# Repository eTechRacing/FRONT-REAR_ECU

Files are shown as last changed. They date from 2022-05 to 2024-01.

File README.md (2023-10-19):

# SHIELD

ADCAN files moved to ADCAN-Legacy branch

_Pendent de publicar en angles

La shield ha de ser una placa versàtil i robusta que serveixi per implementar fàcilment elements comuns que comparteixen diverses plaques. L’avantatge d’implementar una shield és la de disposar d’una base coneguda, provada i fiable per, 
a partir d’ella, implementar qualsevol altre sistema que s’hagi d’incloure dins del cotxe.
Les funcionalitats de la placa shield passen, principalment, per una alimentació estable i constant i per un bus de comunicacions amplament validat i funcional. 
Tot això rodejant d’un microcontrolador molt consistent encarregat de l’adquisició, el processament i l’enviament de dades.

Requisits:
-Alimentació a 5 V i 3.3 V a partir de LV
-Comunicació via CAN1 i CAN2
-Connectors plug-and-play
-MCU potent (STM23)
-Documentació
-Reduir EMIs i soroll amb un bon disseny

El conntector entre la shield i la carrier és una de les parts fonamentals de la placa. La idea és que hi hagi connexió electrica i mecànica entre elles.
S'opta per un connector board-to-board tipus pin header (fabricant Würth) ja que dona la opció d'encaixar una placa sobre l'altre i, a mes, de disposar de totes les connexions
amb un connector senzill de posar i treure.

El microcontrolador és el més potent que s'ha pogut aconseguir per patrocinadors. Més concretament el STM32F777VI6T que compleix de sobres tots els requisits. De totes maneres,
pensant en el fet de que la shield sigui una placa amb futur, s'afageix una memoria EEPROM utilitzat el I2C número 4 del STM32.

Pel que fa la resta de la placa no hi ha cap complicació. S'implementa un USB_OTG amb un connector micro USB 2.0 per debug i visualització de dades per PC. Es fa servir el CAN
transceiver MCP2551 de microchip (fàcil d'aconseguir per samples) i unes proteccions i filtres a la linea CAN bastant estàndard. La resta dels pins del MCU van directament al
pin header excepte:
-VBAT: es col·loca un divisor de tensió rebaixant 30V a 3.3V. Això permet fer servir VBAT com una entrada analogica per medir la tensió que ofereix la LV.
-VBUS: es fa servir com a entrada digital per detectar si hi ha presencia d'USB.
-NRST: pin de reset del micocontrolador. Necessari per programar. Se li posa un botó per també poder fer reset manualment.
-Boot0: se li posa un switch per curtcircuitar a 3.3V o a GND. Això permetrà setejar al micro com a blank i poder carregar informació des del USB o programar més facilment.

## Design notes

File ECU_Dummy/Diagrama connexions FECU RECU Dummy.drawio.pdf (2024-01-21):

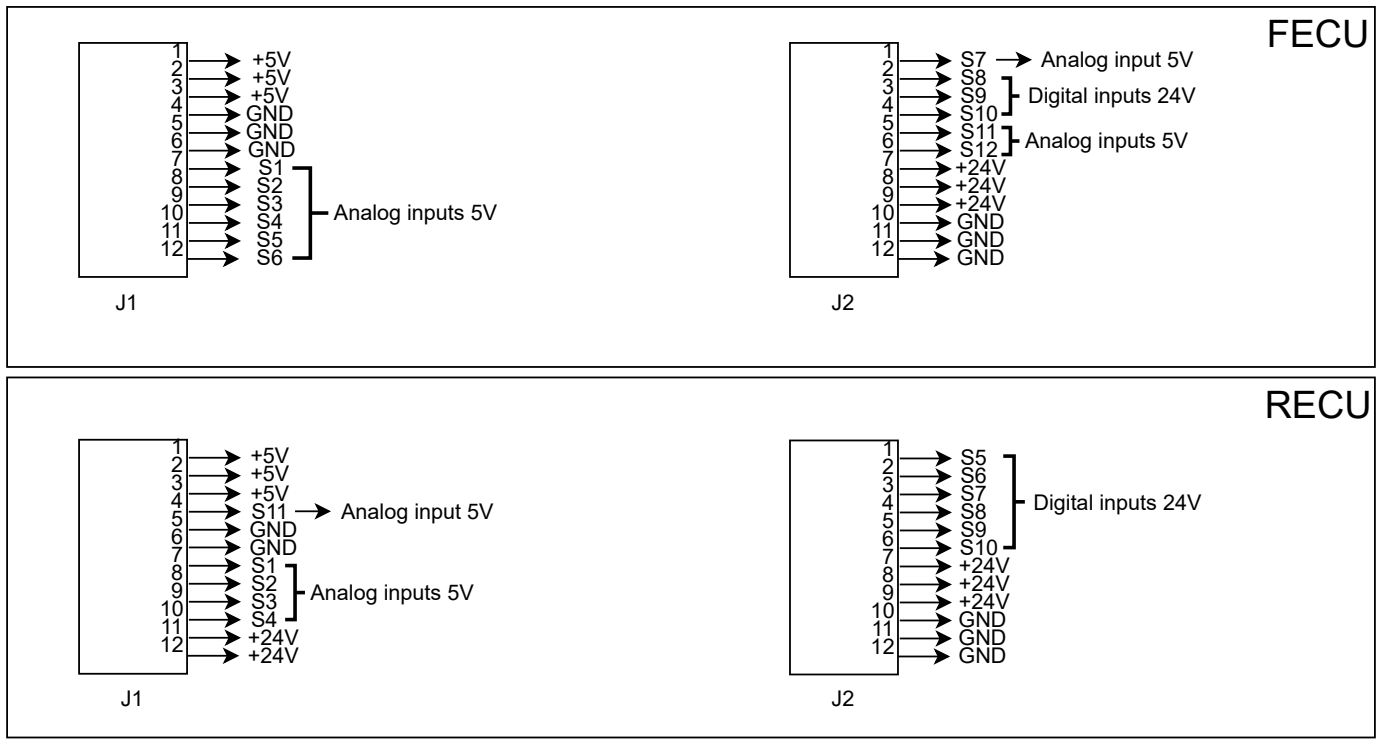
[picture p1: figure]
FECU; RECU; +5V +5V +5V GND GND GND S1 S2 S3 S4 S5 S6; Analog inputs 5V; S7 S8 S9 S10 S11 S12 +24V +24V +24V GND GND GND; Digital inputs 24V; S5 S6 S7 S8 S9 S10 +24V +24V +24V GND GND GND; +5V +5V +5V S11 GND GND S1 S2 S3 S4 +24V +24V; Analog input 5V
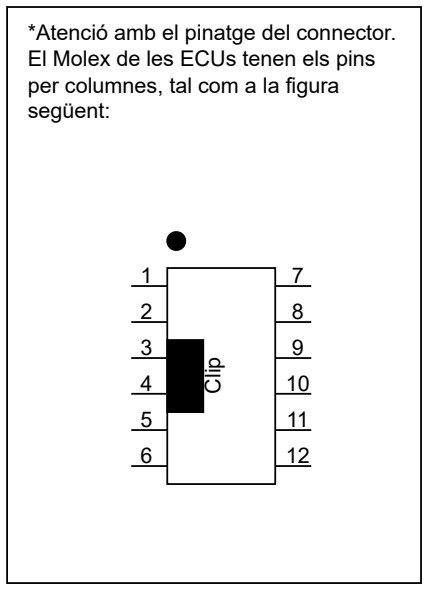
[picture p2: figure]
*Atenció amb el pinatge del connector. El Molex de les ECUs tenen els pins per columnes, tal com a la figura següent:; Clip

Taula connexions connectors des de les ECUs a ECU Dummy:

FRONT ECU

-J1 va a JFS1
-J2 va a JFRS2

REAR ECU

-J1 va a JRS1
-J2 va a JFRS2

*El connector JFRS2 es compatible amb el J2 de les dos ECUs. Nomes n'hi ha un a la ECU_Dummy per tant només es pot fer test del J2 a una ECU alhora

# ECUs & ECU_Dummy interconnections

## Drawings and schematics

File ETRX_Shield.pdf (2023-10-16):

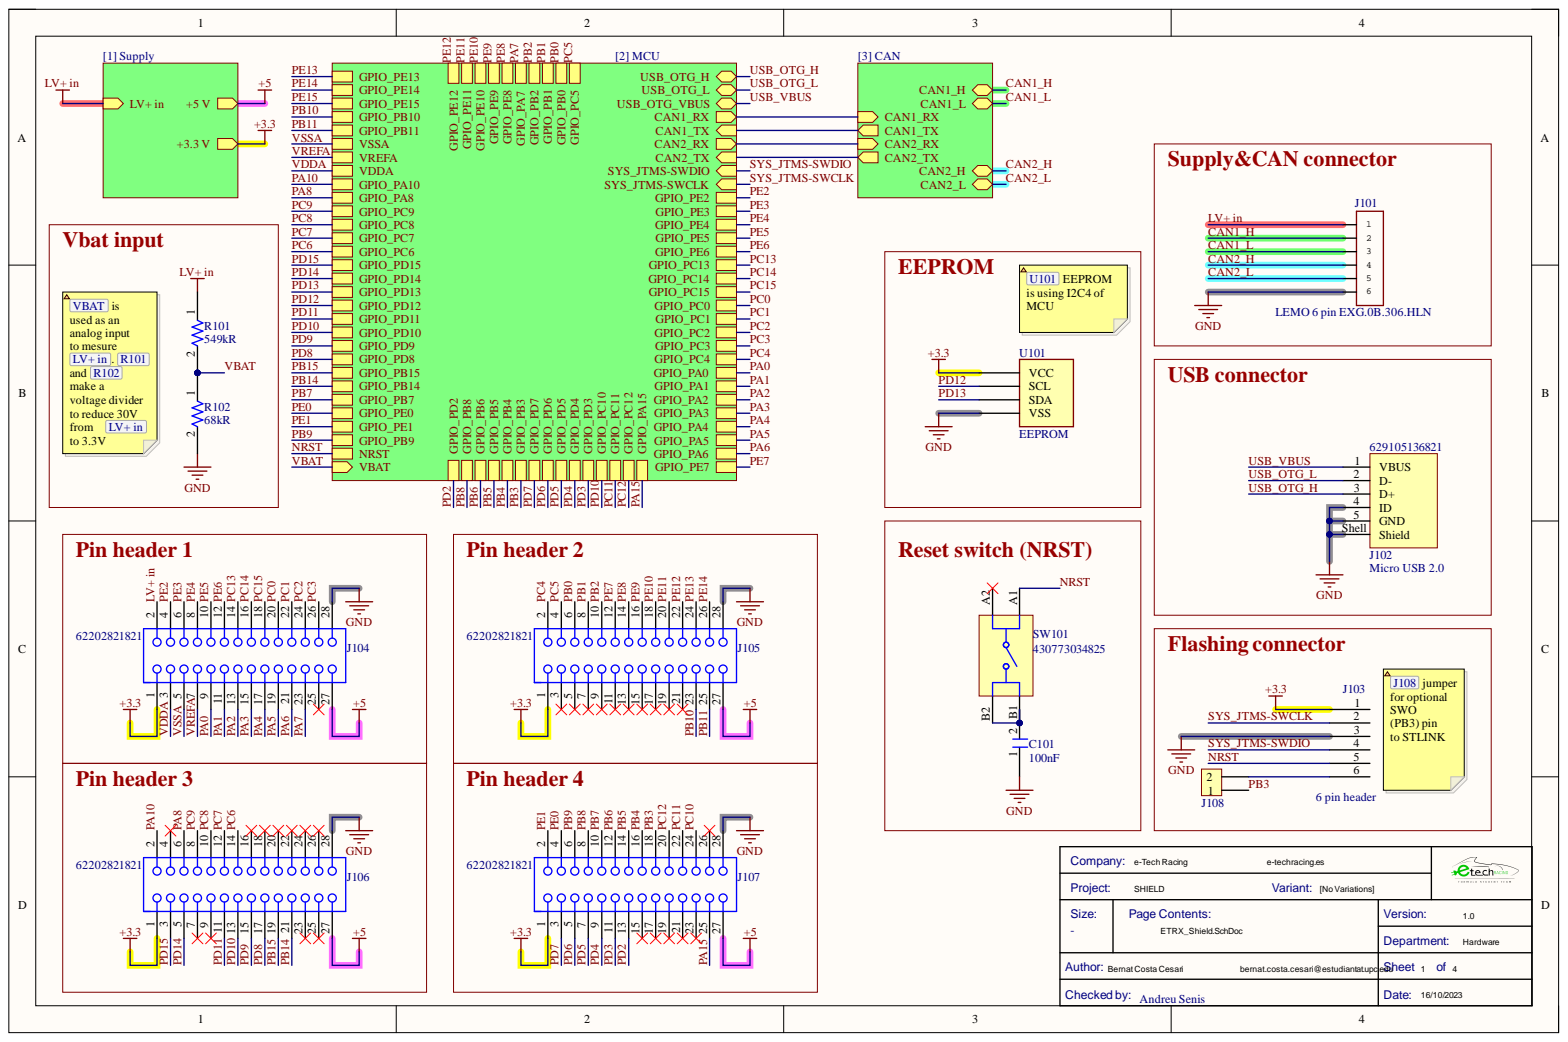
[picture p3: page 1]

LEMO 6 pin EXG.0B.306.HLN

Author: BernatCosta Cesari bernat.costa.cesari@estudiantat.upc.edu | Sheet 1 of 4

Checked by: Andreu Senis | Date: 16/10/2023

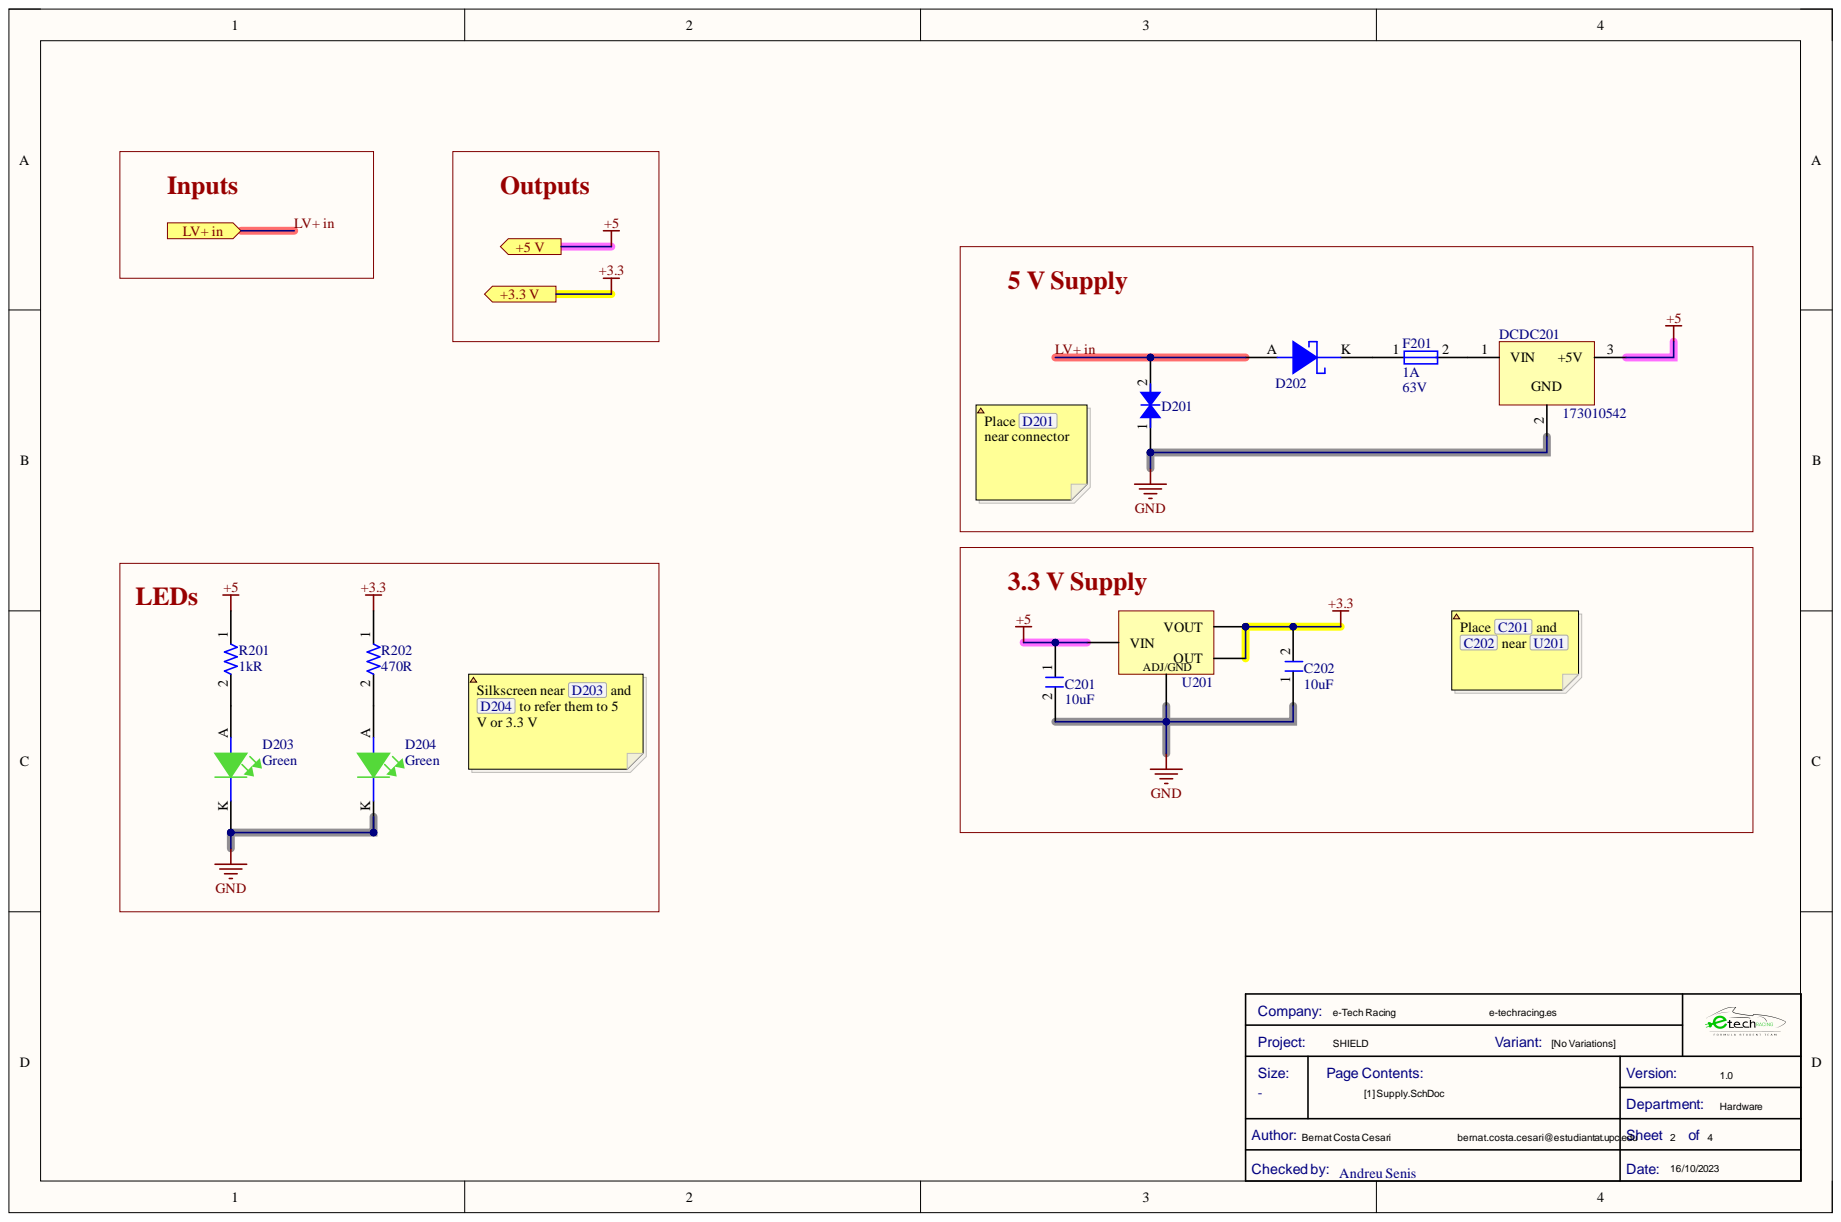
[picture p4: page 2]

Silkscreen near D203 and
D204 to refer them to 5

bernat.costa.cesari@estudiantat.upc.edu

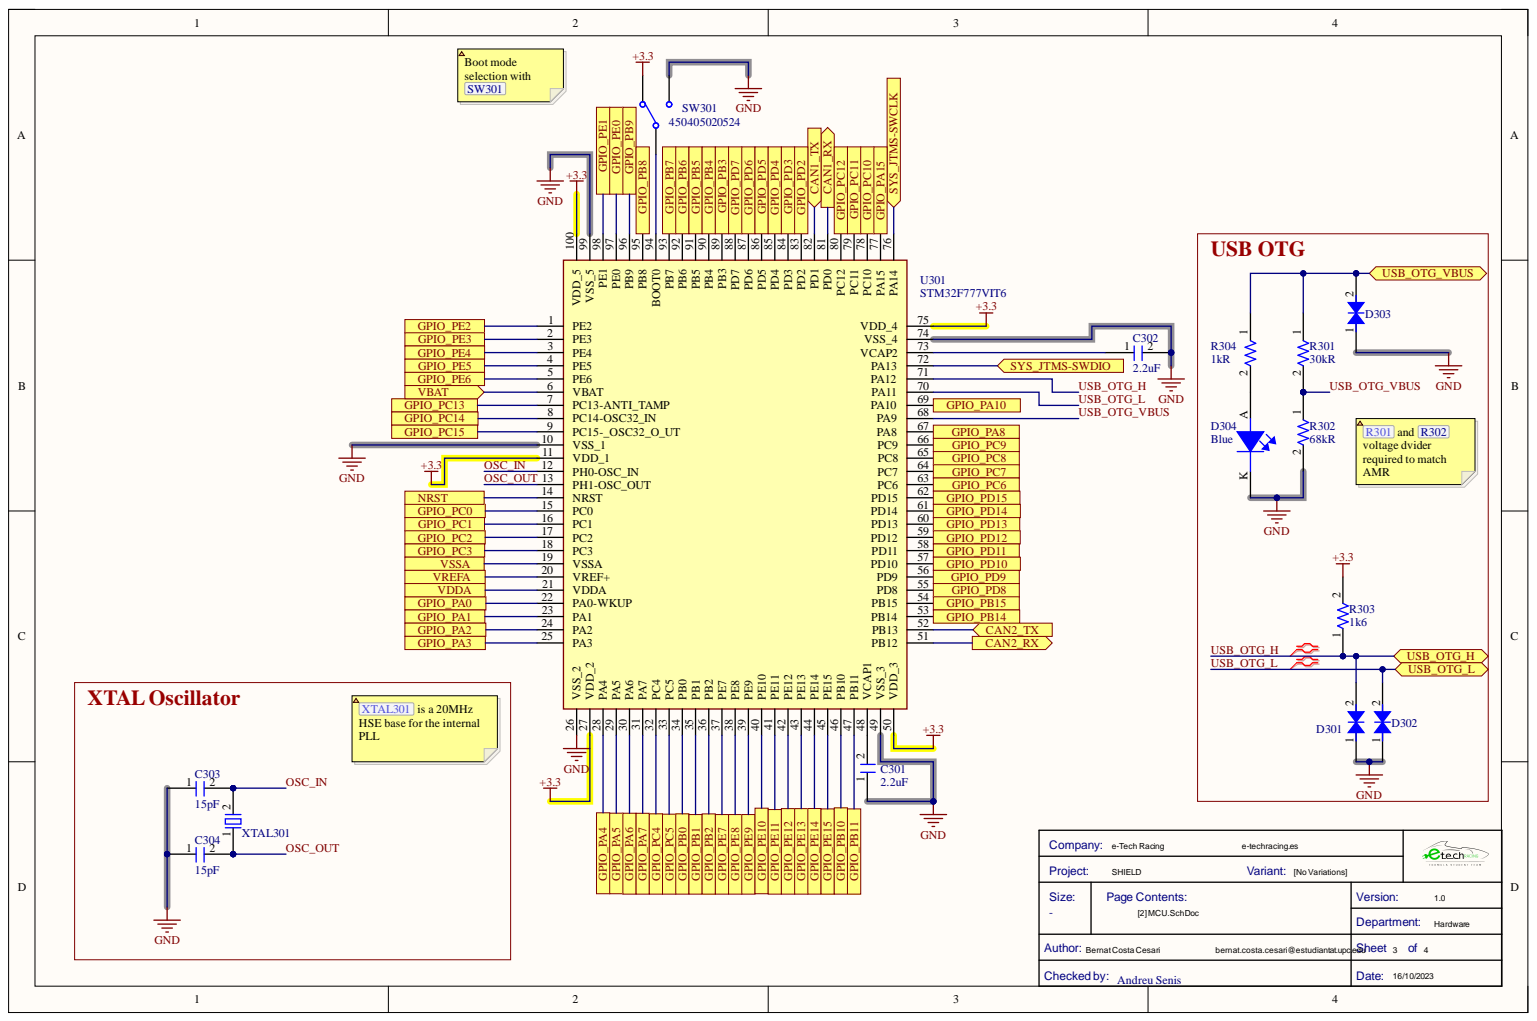
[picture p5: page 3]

GPIO_PC15 | | GPIO_PA8

VDD_1 11

OSC_IN | PH0-OSC_IN 12

GPIO_PC3 | GPIO_PD11
VSSA | GPIO_PD10

XTALOscillator | XTAL301 is a 20MHz HSE base for the internal PLL C303

Author: BernatCosta Cesari bernat.costa.cesari@estudiantat.upc.edu | Sheet 3 of 4

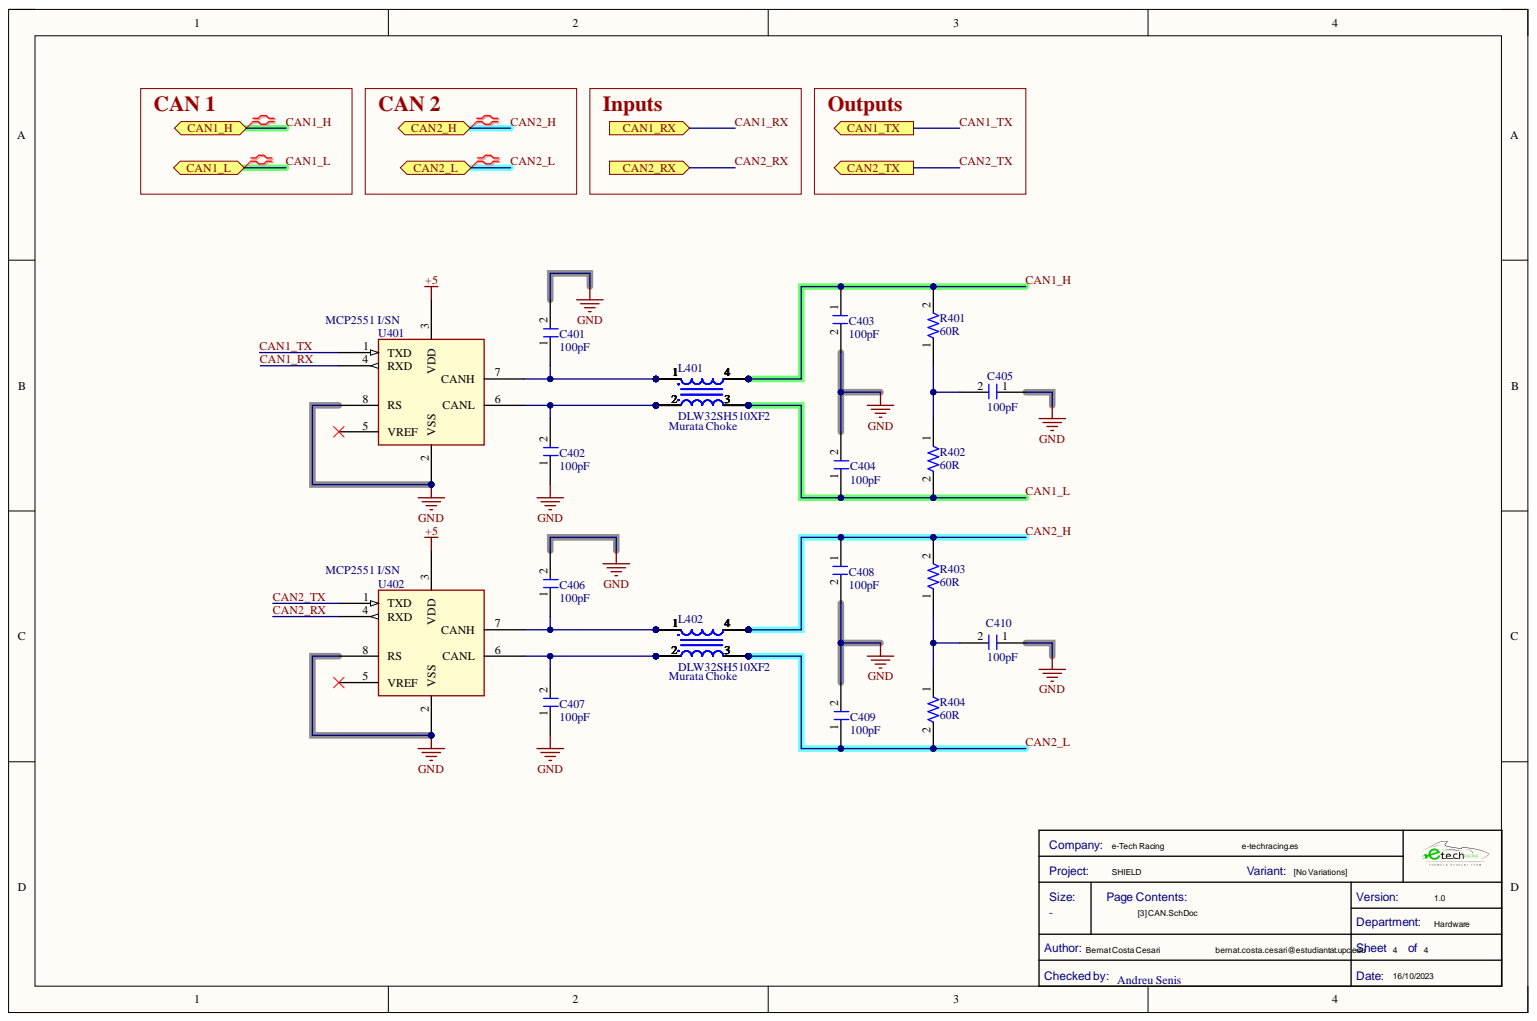
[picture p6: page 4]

bernat.costa.cesari@estudiantat.upc.edu

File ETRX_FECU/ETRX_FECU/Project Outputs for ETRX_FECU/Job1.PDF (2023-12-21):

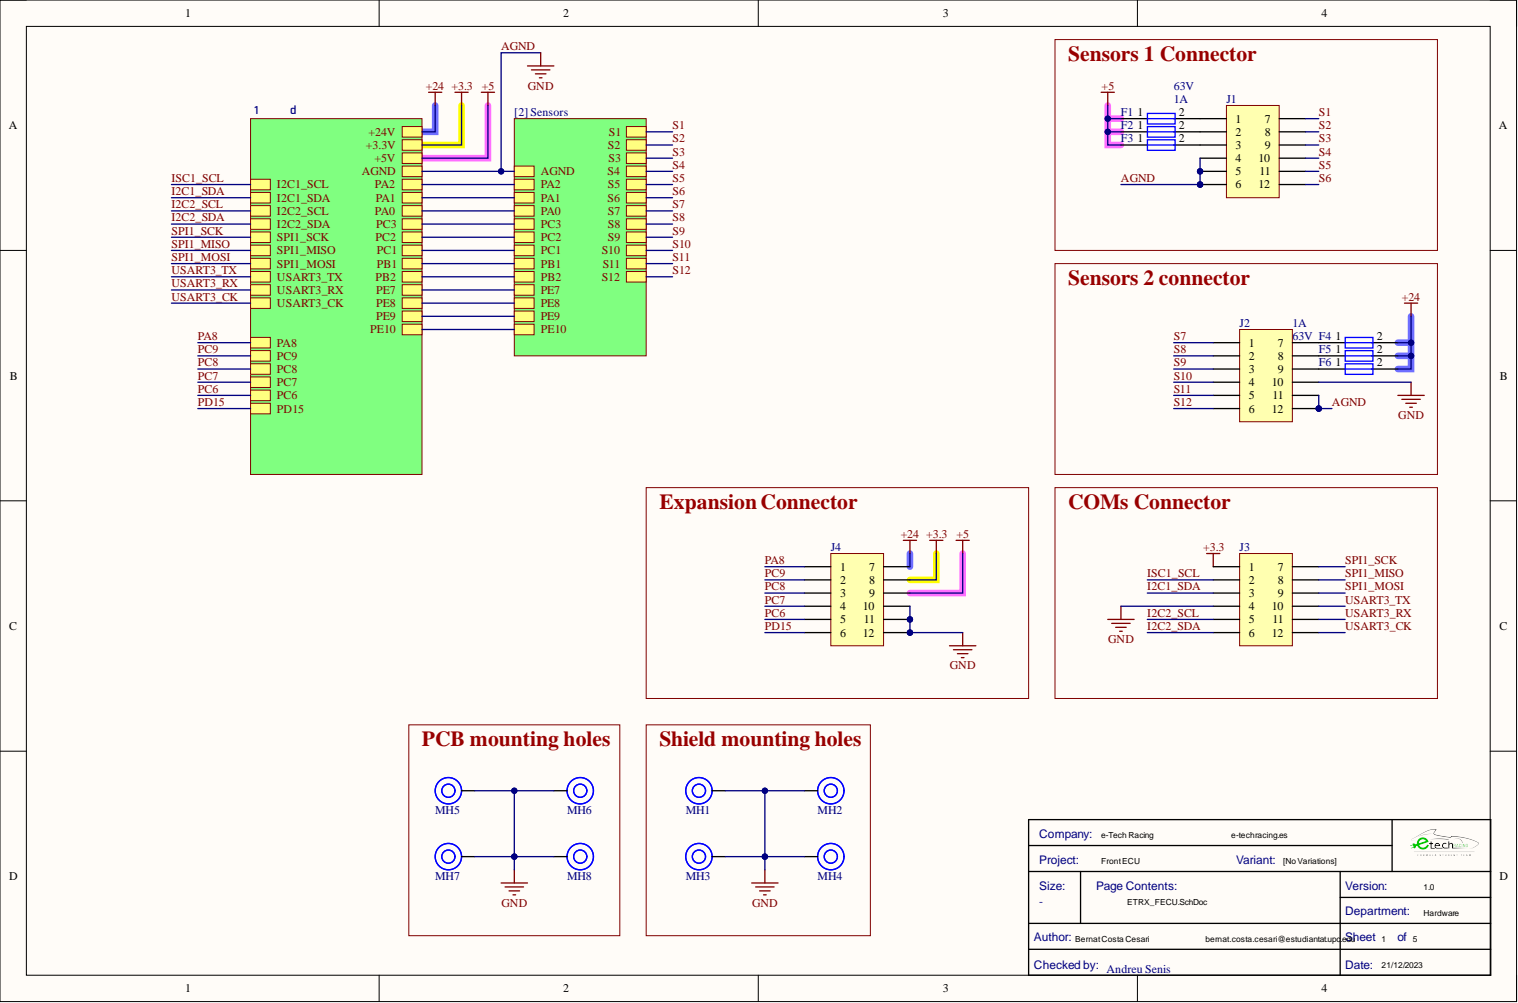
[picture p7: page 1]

F2 1 | 2
F3 1 | 2

Author: BernatCosta Cesari bernat.costa.cesari@estudiantat.upc.edu | Sheet 1 of 5

Checked by: Andreu Senis | Date: 21/12/2023

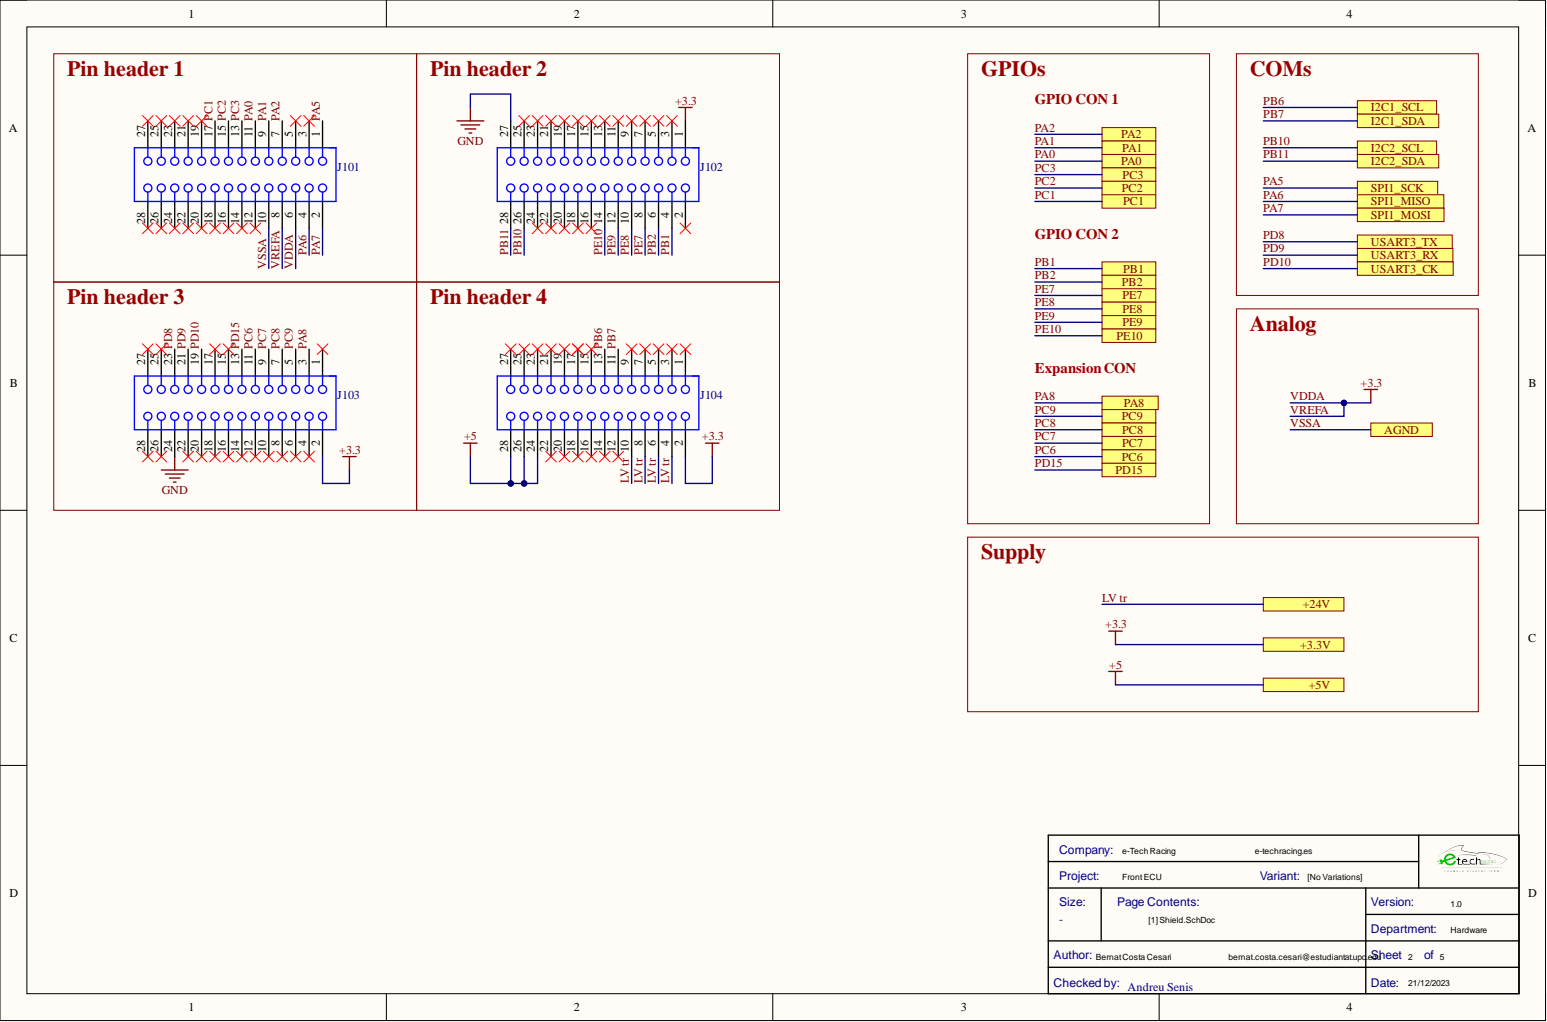
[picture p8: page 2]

Author : B e r n a t C o s t a C e s a ri b e r n a t . c o s t a . c e s a r i @ e s t u d i a n ta t . u p c | . e Shee d u t 2 o f 5

Chec ked by : A n dreu Sen i s | Dat e : 2 1 / 1 2 /2 0 2 3

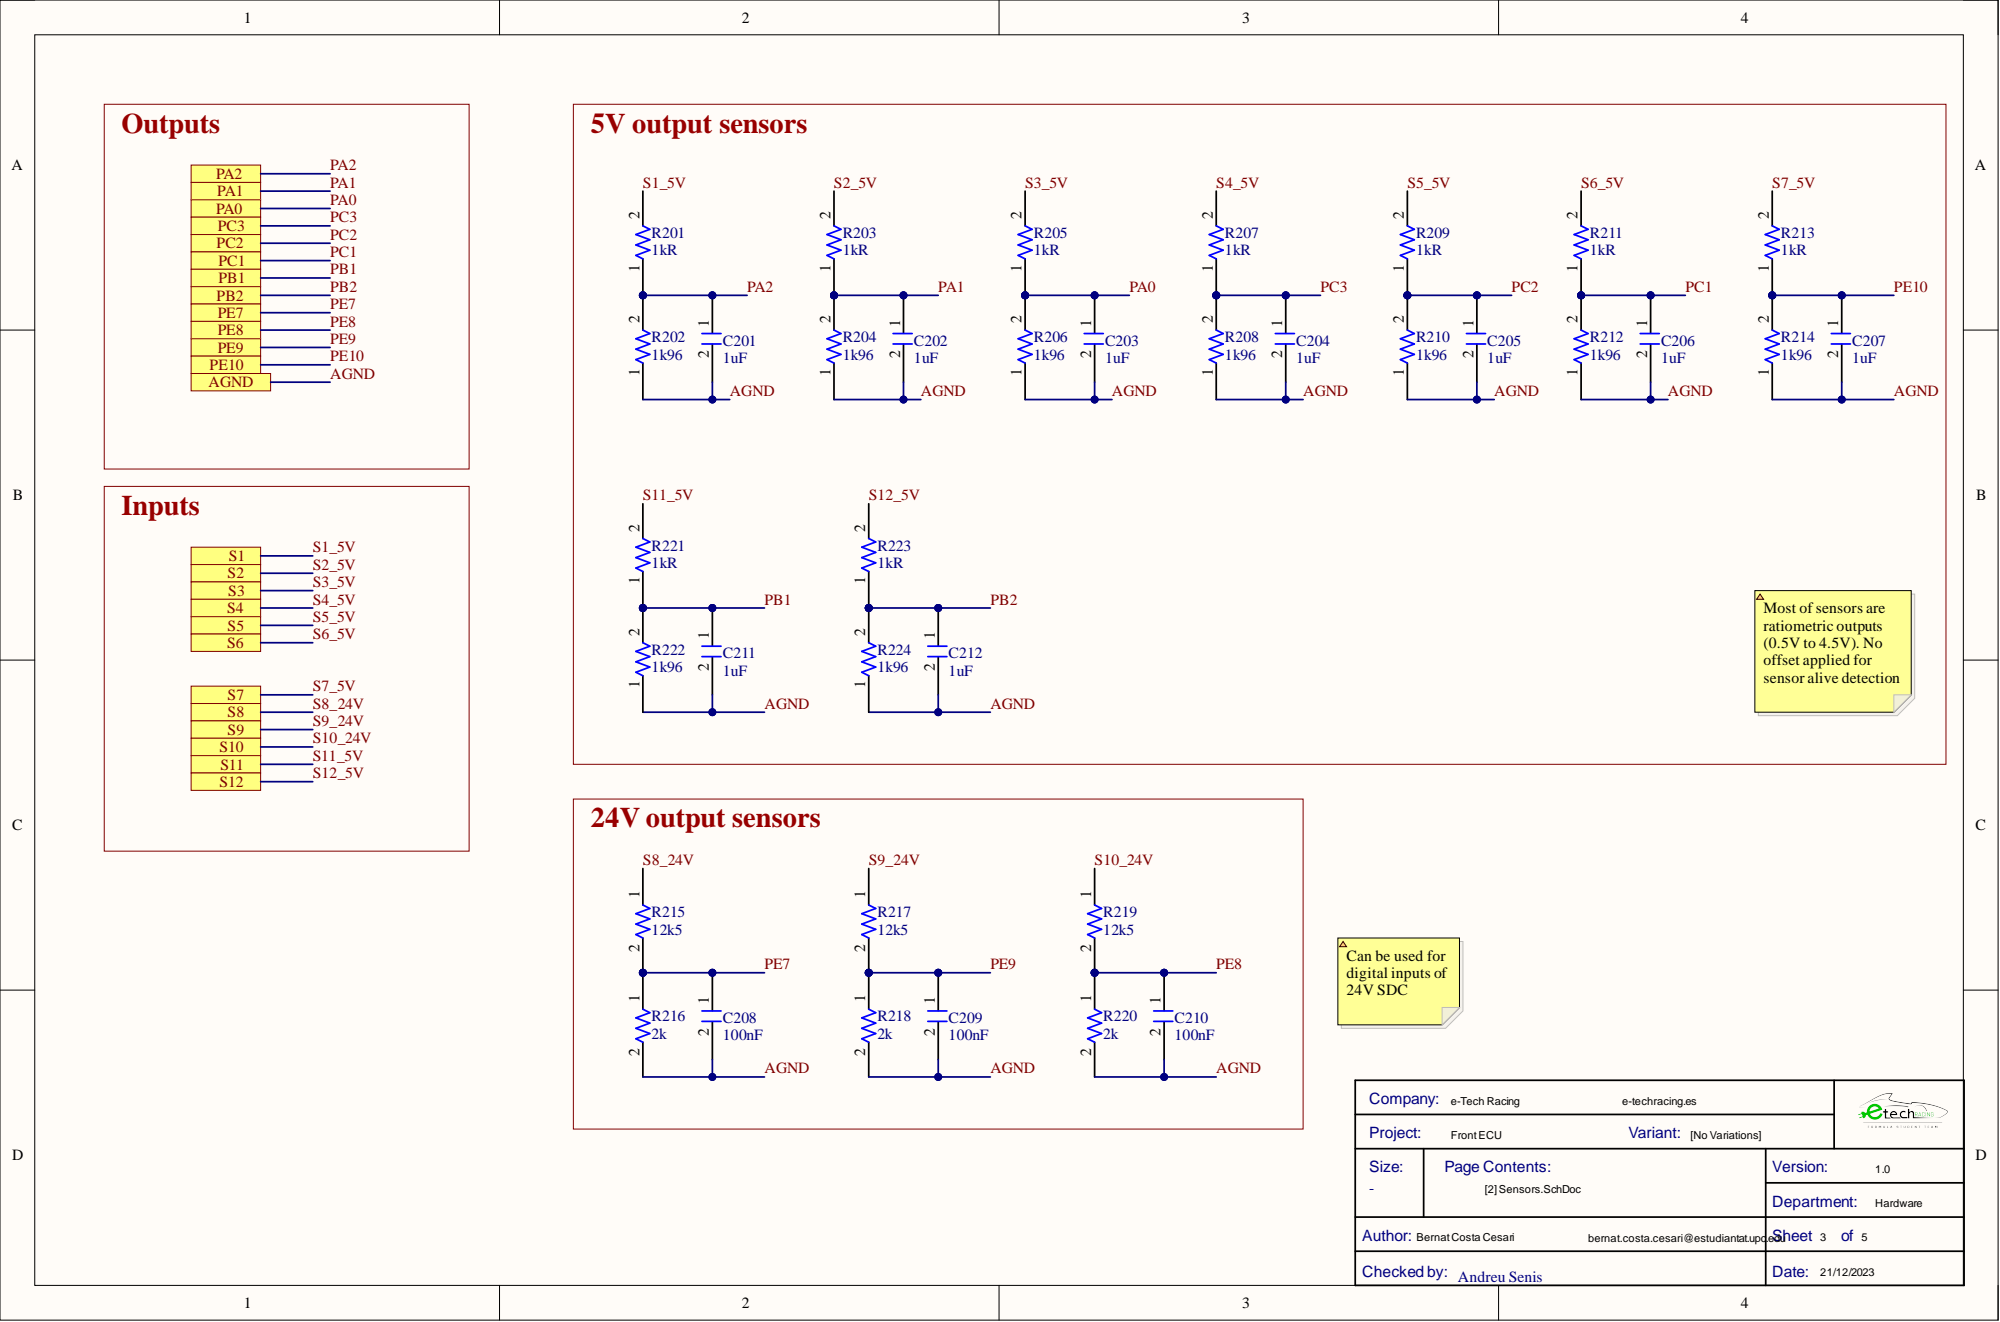
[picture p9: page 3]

Author : B e r n a t C o s t a C e s a ri b e r n a t . c o s t a . c e s a r i @ e s t u d i a n ta t . u p c | . e Shee d u t 3 o f 5

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

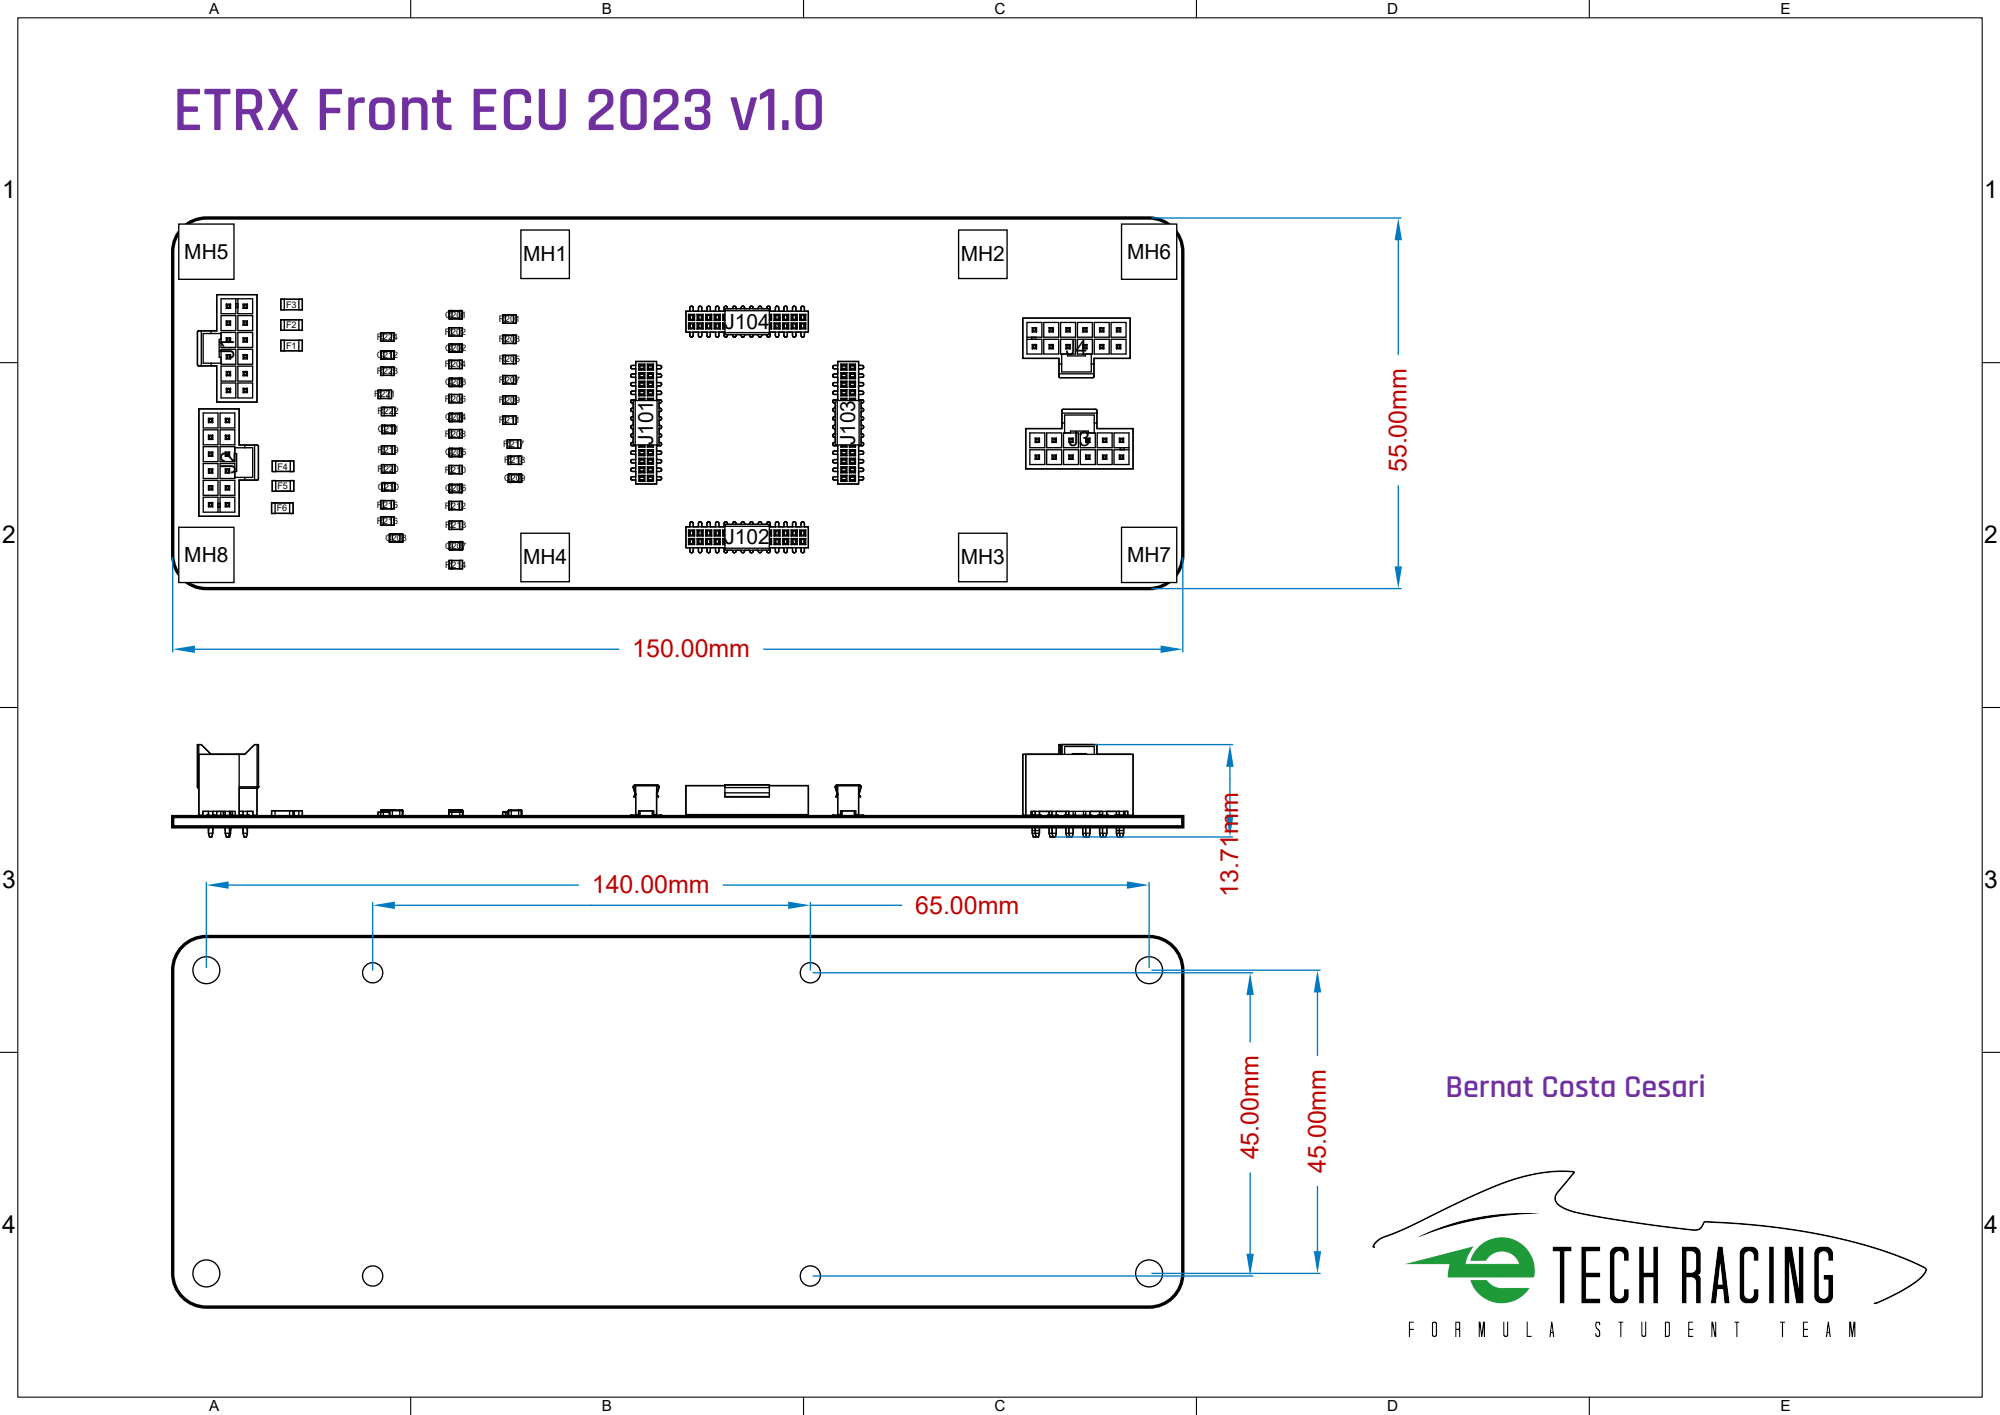
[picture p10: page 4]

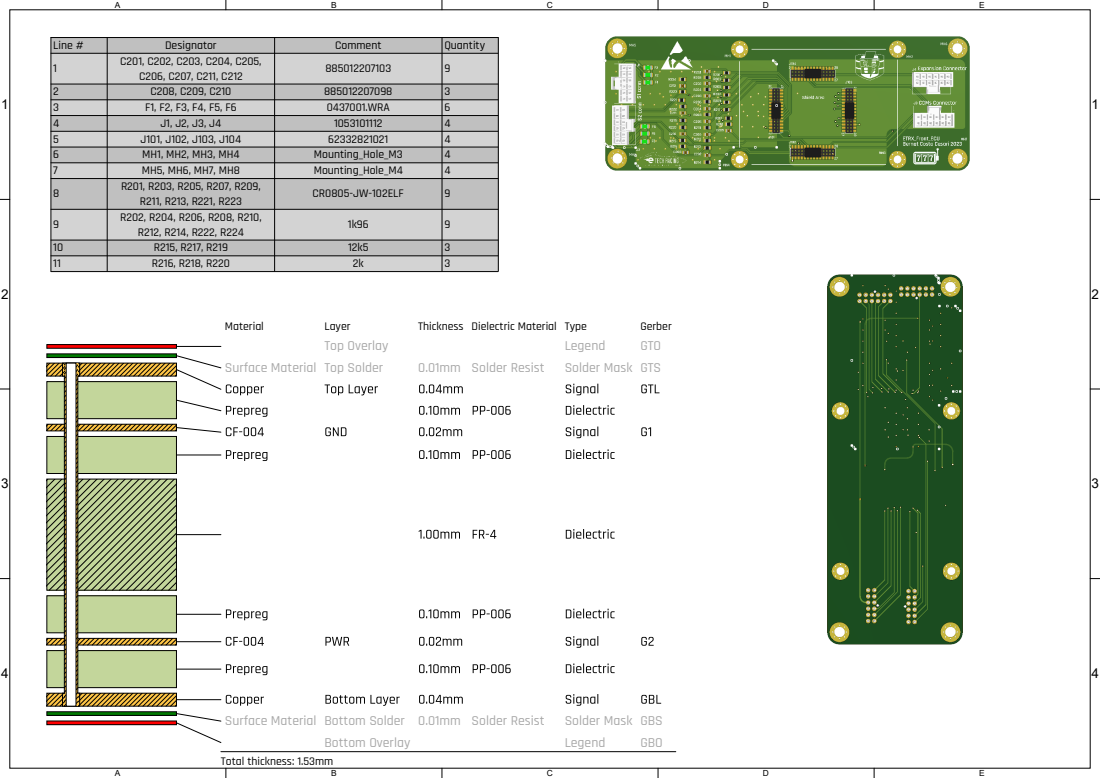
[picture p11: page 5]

Line # | Designator | Comment | Quantity
1 | C201, C202, C203, C204, C205, C206, C207, C211, C212 | 885012207103 | 9

2 | C208, C209, C210 | 885012207098 | 3
3 | F1, F2, F3, F4, F5, F6 | 0437001.WRA | 6
4 | J1, J2, J3, J4 | 1053101112 | 4
5 | J101, J102, J103, J104 | 62332821021 | 4
6 | MH1, MH2, MH3, MH4 | Mounting_Hole_M3 | 4
7 | MH5, MH6, MH7, MH8 | Mounting_Hole_M4 | 4
8 | R201, R203, R205, R207, R209, R211, R213, R221, R223 | CR0805-JW-102ELF | 9

10 | R215, R217, R219 | 12k5 | 3
11 | R216, R218, R220 | 2k | 3

Surface Material Bottom Solder 0.01mm Solder Resist Solder Mask GBS

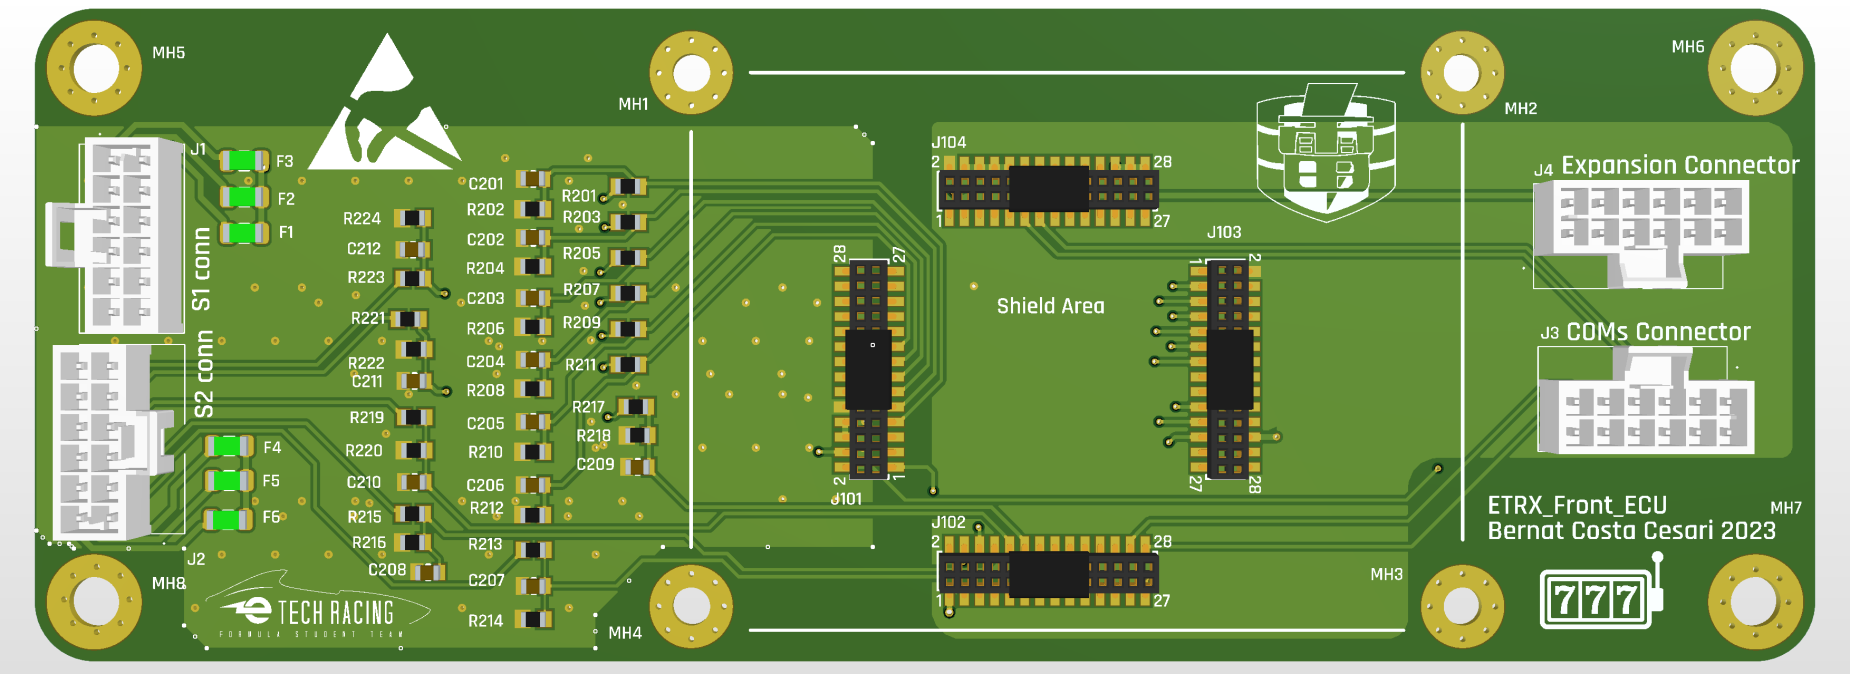
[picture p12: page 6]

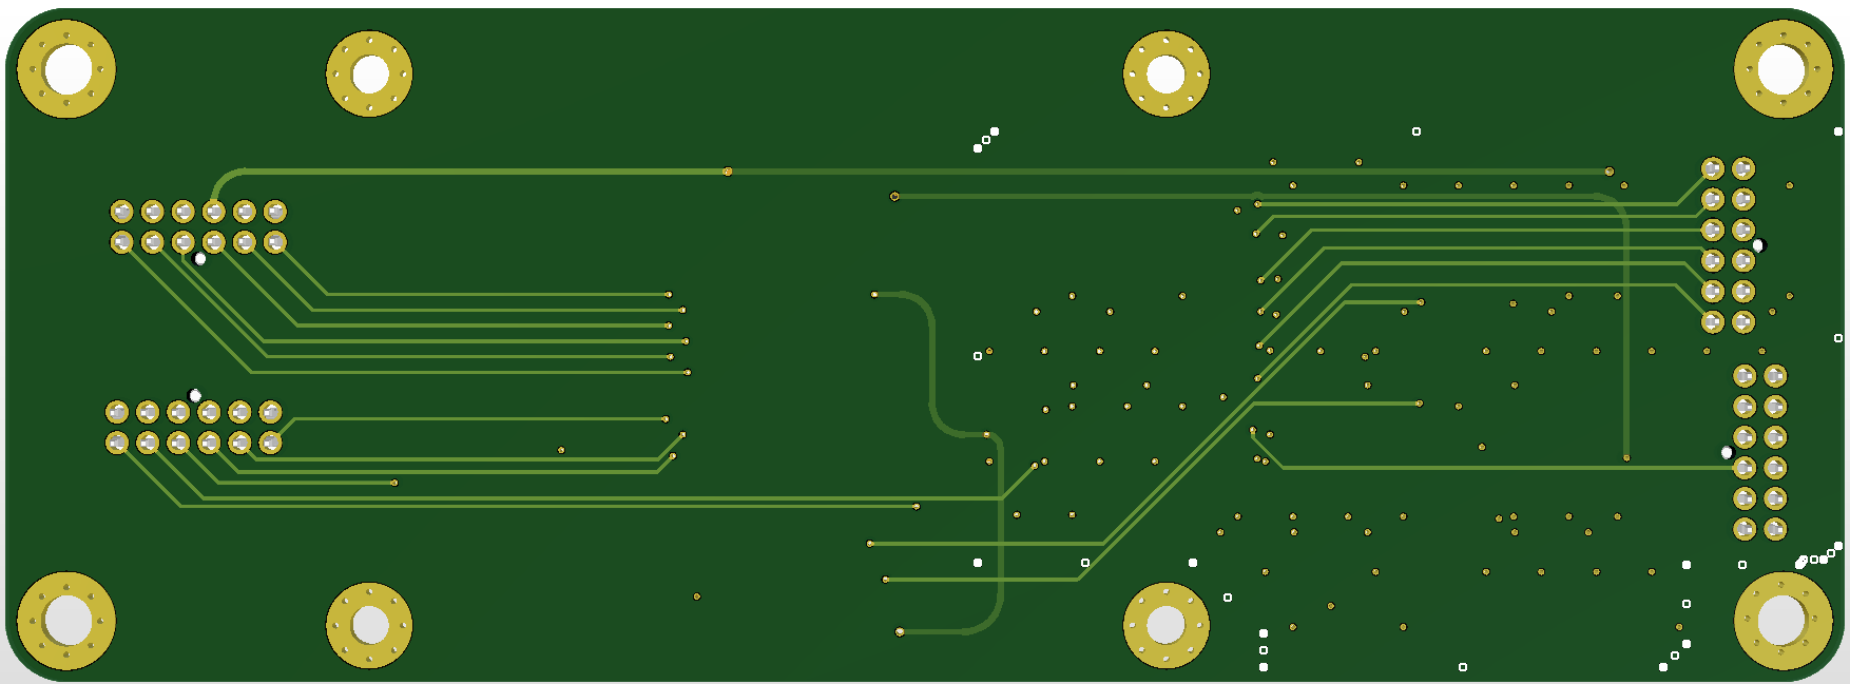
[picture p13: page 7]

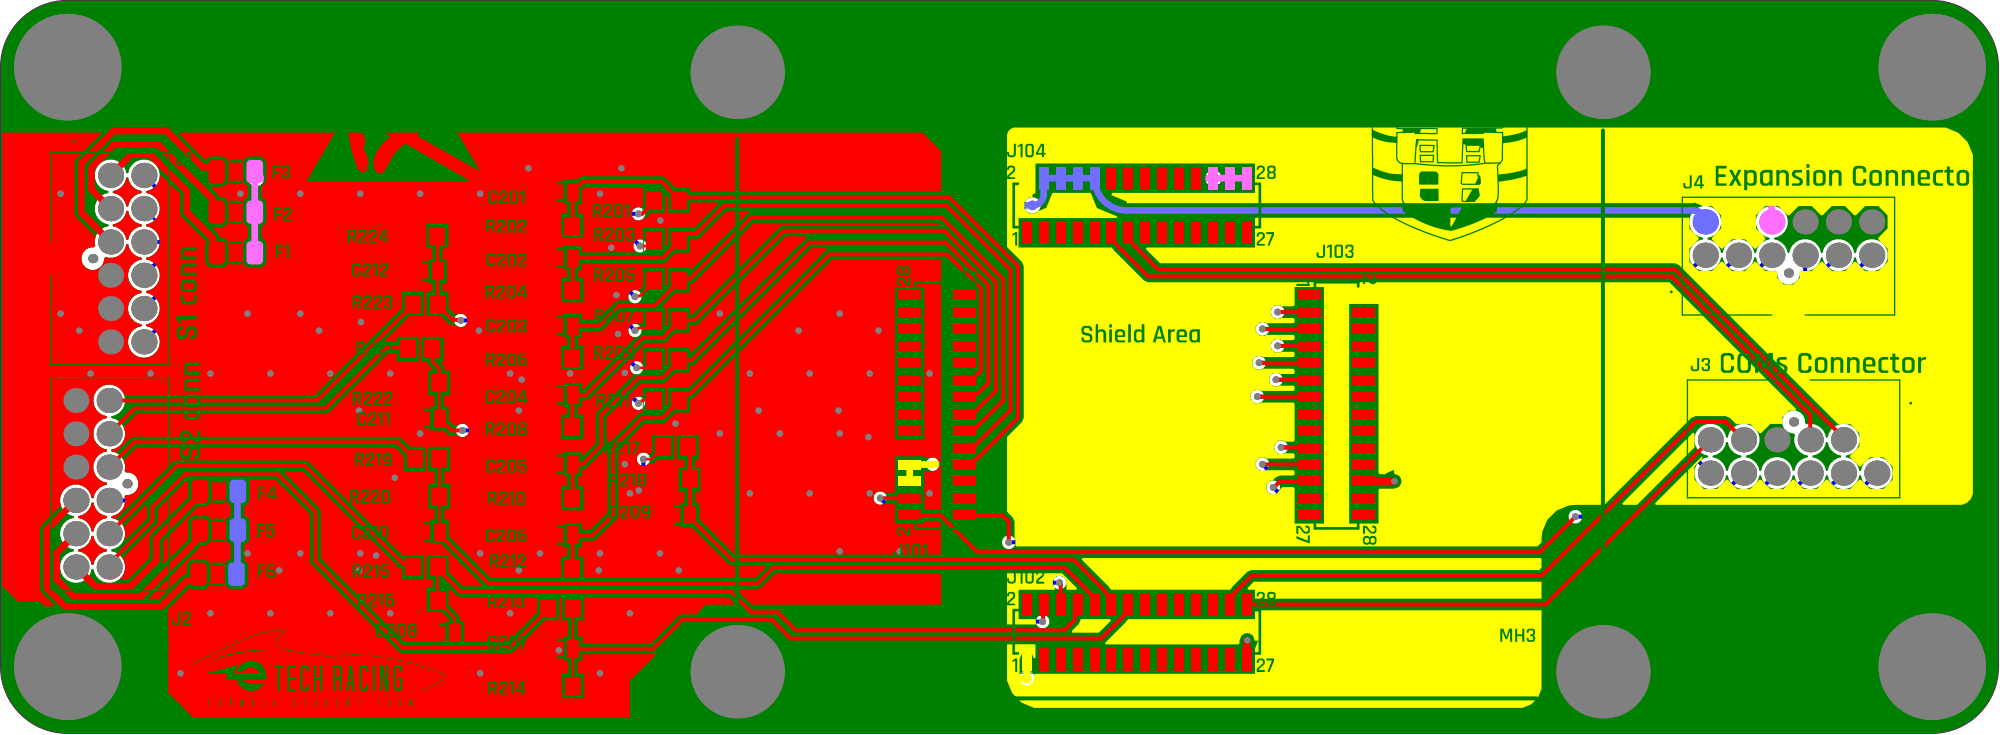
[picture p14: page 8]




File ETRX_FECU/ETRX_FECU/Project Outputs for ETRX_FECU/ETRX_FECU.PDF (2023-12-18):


F2 1 | 2
F3 1 | 2

Author: BernatCosta Cesari bernat.costa.cesari@estudiantat.upc.edu | Sheet 1 of 5

Checked by: Andreu Senis | Date: 18/12/2023


Author : B e r n a t C o s t a C e s a ri b e r n a t . c o s t a . c e s a r i @ e s t u d i a n ta t . u p c | . e Shee d u t 2 o f 5

Chec ked by : A n dreu Sen i s | Dat e : 1 8 / 1 2 /2 0 2 3


Author : B e r n a t C o s t a C e s a ri b e r n a t . c o s t a . c e s a r i @ e s t u d i a n ta t . u p c | . e Shee d u t 3 o f 5

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



Line # | Designator | Comment | Quantity
1 | C201, C202, C203, C204, C205, C206, C207, C211, C212 | 885012207103 | 9

2 | C208, C209, C210 | 885012207098 | 3
3 | F1, F2, F3, F4, F5, F6 | 0437001.WRA | 6
4 | J1, J2, J3, J4 | 1053101112 | 4
5 | J101, J102, J103, J104 | 62332821021 | 4
6 | MH1, MH2, MH3, MH4 | Mounting_Hole_M3 | 4
7 | MH5, MH6, MH7, MH8 | Mounting_Hole_M4 | 4
8 | R201, R203, R205, R207, R209, R211, R213, R222, R224 | CR0805-JW-102ELF | 9

10 | R215, R217, R219 | 12k5 | 3
11 | R216, R218, R220, R221, R223 | 2k | 5

Surface Material Bottom Solder 0.01mm Solder Resist Solder Mask GBS







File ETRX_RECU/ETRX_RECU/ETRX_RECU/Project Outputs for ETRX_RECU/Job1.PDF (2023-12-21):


F2 1 | 2
F3 1 | 2

Author: BernatCosta Cesari bernat.costa.cesari@estudiantat.upc.edu | Sheet 1 of 4

Checked by: Andreu Senis | Date: 21/12/2023








Line # | Designator | Comment | Quantity
1 | C201, C202, C203, C204, C211, C301, C302, C303, C304, C305 | 885012207103 | 10

3 | F1, F2, F3, F4, F5, F6, F7, F8 | 0437001.WRA | 8
4 | J1, J2, J3, J4 | 1053101112 | 4
5 | J101, J102, J103, J104 | 62332821021 | 4
6 | MH1, MH2, MH3, MH4 | Mounting_Hole_M3 | 4
7 | MH5, MH6, MH7, MH8 | Mounting_Hole_M4 | 4
8 | Q301, Q302, Q303 | BC817-25LT1G | 3
9 | R201, R203, R205, R207, R221, R301, R303, R305, R307, R309 | CR0805-JW-102ELF | 10

13 | R302, R304, R306 | CR0805-JW-103ELF | 3

Surface Material Bottom Solder 0.01mm Solder Resist Solder Mask GBS

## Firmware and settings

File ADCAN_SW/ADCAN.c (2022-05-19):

/* *************************************************************************************************
**  File Name    : ADCAN.c
**  Description  : ADC conversion (microcontroller PIC18F2685) and CAN communication (MCP2561) with 
               multiple analog sensors (refer to Sensorics design) 
** ************************************************************************************************/

#include "ADCAN.h"
#include "ADCAN_vars.c"
#include "ADCAN_funs.c"

void main()
{
   //configuracio inicial programa
   Initial_Config(); //configuracio inicial del micro
   delay_ms(5);

   enable_interrupts(INT_TIMER2);
   enable_interrupts(GLOBAL);

   setup_timer_2(T2_DIV_BY_4,250,5); //overflow cada 1.0 ms

   delay_ms(3);

   enable_interrupts(int_canrx0);  

   while (true)
   {
      output_high(LED1); //led comprovacio comunicacio del micro

      if (RXB0CON.RXFUL == 1)
      {
         RXB0CON.RXFUL = 0;      // si no es gestionen els missatges
         //CANFLAG0=1;           // si es gestionen els missatges
      }
      if (RXB1CON.RXFUL == 1)
      {
         RXB1CON.RXFUL = 0;      // si no es gestionen els missatges
         //CANFLAG1=1;           // si es gestionen els missatges
      }

      // CAN SINCRONISM
      if (CAN_flag == 1)         //quan CAN_flag s'hagi activat ...
      {
         CAN_flag = 0;           //reinicia variable
         contCAN++;              //comptador de CAN_flag per enviar alive

         if ( not_first_message == 1 )
         {  
            // SEND ALIVE
            if (contCAN >= 4)   //quan CAN_flag s'hagi activat 4 vegades ...
            {
               send_alive(0xB0); //enviar senyal per indicar que el node no esta penjat
            }  

            send_data (0x85,8,APPS2,APPS1,SteeringSensor,BrakeSensor); //envia dades sensors corresponents per CAN
            send_data (0x86,4,SUSPFL,SUSPFR,0,0); //envia dades sensors corresponents per CAN

         } // END if (not_first_message == 1)         

      not_first_message = 1;      //variable per no enviar les dades quan el primer CAN_flag

      } // END CAN_flag


      if ( read_ADC_flag>0 ) //cada 1ms
      {    

         enable_interrupts(INT_TIMER2); //reinicia timer2
         read_ADC_flag = 0;

         //es llegeixen les dades de cada sensor cada 1 ms, cada 8 dades es sumen en la variable sensor_sum (s'esta fent una funcio)
         
         // APP1
         set_adc_channel(0);
         delay_us(20);
         //SUMA = read_adc();
         //APPS1_sum += SUMA;
         APPS1 = read_adc();

         // APP2
         set_adc_channel(1);
         delay_us(20);
         //SUMA = read_adc();
         //APPS2_sum += SUMA;
         APPS2 = read_adc();

         // Brake           
         set_adc_channel(2);
         delay_us(20);
         //SUMA = read_adc();
         //BrakeS_sum += SUMA;
         BrakeSensor = read_adc();

         // Steering
         set_adc_channel(3);
         delay_us(20);
         //SUMA = read_adc();        
         //Steering_sum += SUMA;
         SteeringSensor = read_adc();

         // Spring FR
         set_adc_channel(10);
         delay_us(20);
         //SUMA = read_adc();
         //SpringFR_sum += SUMA;
         SUSPFL = read_adc();

         // Spring FL 
         set_adc_channel(8);
         delay_us(20);
         //SUMA = read_adc();
         //SpringFL_sum += SUMA;
         SUSPFR = read_adc();

         output_high(LED2); //led comprovacio conversió ADC 


/*         if ( mean_filter_flag < 8 )
         {
            enable_interrupts(INT_TIMER2);
         }
         else //cada 8 ms
         {
            enable_interrupts(INT_TIMER2);
            mean_filter_flag = 0;

            //filtre per cada senyal (s'esta fent una funcio)   
            APPS1_sum = APPS1_sum >> 3;           
            APPS1 = ((APPS1_sum<<8)&0xFF00)+((APPS1_sum>>8)&0x00FF);            

            APPS2_sum = APPS2_sum >> 3;            
            APPS2 = ((APPS2_sum<<8)&0xFF00)+((APPS2_sum>>8)&0x00FF);               

            BrakeS_sum = BrakeS_sum >> 3;
            BrakeSensor = ((BrakeS_sum<<8)&0xFF00)+((BrakeS_sum>>8)&0x00FF);            

            Steering_sum = Steering_sum >> 3;           
            SteeringSensor = ((Steering_sum<<8)&0xFF00)+((Steering_sum>>8)&0x00FF);  

            SpringFR_sum = SpringFR_sum >> 3;
            SUSPFR = ((SpringFR_sum<<8)&0xFF00)+((SpringFR_sum>>8)&0x00FF);            

            SpringFL_sum = SpringFL_sum >> 3;
            SUSPFL = ((SpringFL_sum<<8)&0xFF00)+((SpringFL_sum>>8)&0x00FF);

            //reinicialitzacio variables sensor_sum (s'esta fent una funcio)
            APPS1_sum = 0;
            APPS2_sum = 0;
            BrakeS_sum = 0;
            Steering_sum = 0;
            SpringFR_sum = 0;
            SpringFL_sum = 0;

         } */
      } // END if (read_adc_flag >0)
   } // END while(1)
} // END Main

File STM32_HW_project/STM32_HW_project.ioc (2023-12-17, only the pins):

Mcu.UserName=STM32F777VITx
PA11.Signal=USB_OTG_FS_DM
PA12.Signal=USB_OTG_FS_DP
PA5.Signal=SPI1_SCK
PA6.Signal=SPI1_MISO
PA7.Signal=SPI1_MOSI
PA9.Signal=USB_OTG_FS_VBUS
PB10.Signal=I2C2_SCL
PB11.Signal=I2C2_SDA
PB12.Signal=CAN2_RX
PB13.Signal=CAN2_TX
PB6.Signal=I2C1_SCL
PB7.Signal=I2C1_SDA
PD0.Signal=CAN1_RX
PD1.Signal=CAN1_TX
PD10.Signal=USART3_CK
PD8.Signal=USART3_TX
PD9.Signal=USART3_RX
PH0/OSC_IN.Signal=RCC_OSC_IN
PH1/OSC_OUT.Signal=RCC_OSC_OUT

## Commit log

2022-03-02 PCB 02_03_22
    [ADCAN.PcbDoc, ADCAN.PrjPCB, ADCAN_21_22_Project.PrjPcb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]
2022-11-29 ADCAN + Accelerometre
    [main.SchDoc]
2022-11-30 Final version PCB
2022-12-09 hardware almost finished
    [ADCAN.PrjPcb, ADCAN.SchDoc, [1] Supply.SchDoc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]
2022-12-11 final version, ready for production
    [ADCAN.GBL, ADCAN.GBO, ADCAN.GBP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]
2023-01-13 no blind vias
    [ADCAN.GBL, ADCAN.GBO, ADCAN.GBP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]
2023-10-16 Create Altium project and updated libraries
    [CAN Transceiver.SchLib, QFP50P1600X1600X160-100N.PcbLib, STM32F777VIT6.SchLib]
2023-10-16 Create ETRX_Shield project
    [ETRX_Shield.PrjPcb, ETRX_Shield.SchDoc, [1] Supply.SchDoc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]
2023-10-16 Removed PD12 and PD13 from pin header 3
    PD12 and PD13 were already used for I2C EEPROM
    [ETRX_Shield.SchDoc]
2023-10-16 Updated ETRX_Shield Schematic
    [CAN Transceiver.SchLib, ETRX_Shield.PrjPcb, ETRX_Shield.SchDoc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]
2023-10-17 Create Provisional BOM.xlsx
    [Provisional BOM.xlsx]
2023-10-17 Update ETRX_Shield_SCH
    [ETRX_Shield.PrjPcb, [2] MCU.SchDoc]
2023-12-11 Create FECU flow diagram and signals excel
    [ETRX_FECU.PcbDoc, ETRX_FECU.PrjPcb, ETRX_FECU.SchDoc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]
2023-12-11 Create RECU flow diagram
2023-12-12 Update ETRX ECU excel documents
    [ETRX_RECU.xlsx, HW_FECU.xlsx]
2023-12-12 Update Altium project and excel documents
    [ETRX_FECU.PrjPcb, ETRX_FECU.SchDoc, HW_FECU.xlsx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]
2023-12-13 Update Altium project
    [ETRX_FECU.PrjPcb, ETRX_FECU.SchDoc, [1] Shield.SchDoc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]
2023-12-15 Update FECU Altium Project
    [ETRX_FECU.PcbDoc, ETRX_FECU.PrjPcb, ETRX_FECU.SchDoc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]
2023-12-17 Update STM32 Project
2023-12-17 FECU ready for testing
    [ETRX_FECU.GBL, ETRX_FECU.GBO, ETRX_FECU.GBP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]
2023-12-18 Create RECU Altium Project
    [ETRX_FECU.GBL, ETRX_FECU.GBO, ETRX_FECU.GBP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]
2023-12-18 Update RECU Altium project
    [ETRX_FECU.SchDoc, ETRX_RECU.PcbDoc, ETRX_RECU.SchDoc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]
2023-12-18 RECU Altium project
    [[3]Power.SchDoc]
2023-12-20 Update Altium projects
    [ETRX_FECU.GBL, ETRX_FECU.GBO, ETRX_FECU.GBP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]
2023-12-21 FECU and RECU ready for production
    [ETRX_FECU.GBL, ETRX_FECU.GBO, ETRX_FECU.GBP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]
2024-01-02 Create BOM for FECU and RECU
    [ETRX_FECU.PrjPcb, ETRX_RECU.PrjPcb]
2024-01-19 Create ECU_Dummy
    [PCB_Project.PrjPcb]
2024-01-19 Update ECU_Dummy
    [ECU_Dummy.SchDoc]
2024-01-21 ECU Dummy Output fabrication
    [ECU_Dummy.GBL, ECU_Dummy.GBO, ECU_Dummy.GBP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]
2024-01-30 Create Diff Pressure Sensor PCB
    [PlacaSensor_MPXV7002.PcbDoc, PlacaSensor_MPXV7002.PrjPcb, PlacaSensor_MPXV7002.SchDoc]
2024-01-31 Update diff pressure sensor PCB
    [PlacaSensor_MPXV7002.SchDoc]
2024-01-31 Update Diff Pressure PCB
    [PlacaSensor_MPXV7002.PcbDoc, PlacaSensor_MPXV7002.SchDoc]
2024-01-31 Diff Pressure Sensor PCB ready for production
    [PlacaSensor_MPXV7002.GBL, PlacaSensor_MPXV7002.GBO, PlacaSensor_MPXV7002.GBP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]
2024-01-31 Xurraca PCB readdy for production
    [PlacaSensor_MPXV7002.GBL, PlacaSensor_MPXV7002.GBO, PlacaSensor_MPXV7002.GBP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]
2024-03-09 Update FECU
    [ETRX_FECU.PrjPcb, ETRX_FECU.SchDoc, [1] Shield.SchDoc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]
